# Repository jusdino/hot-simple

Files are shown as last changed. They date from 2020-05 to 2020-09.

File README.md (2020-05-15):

# hot-simple
Ender 3 Pro hot-end upgrade parts for E3D v6

*Designed in OpenScad*

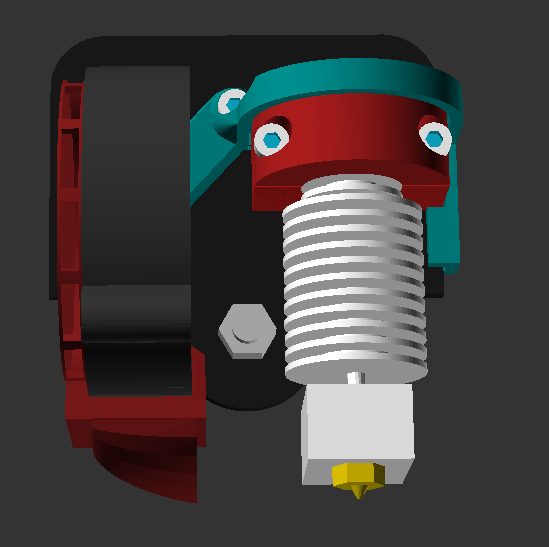
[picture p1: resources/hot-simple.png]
hot-simple


## Overview

This hot-end design is still very much a work in progress but its intent is to be simple but easy to modify. While the design is still quite incomplete, it is functional and I have been using it for a while now, with great results. I will likely eventually post this to thingiverse.com, but haven't yet as it's still too incomplete.

### Current design
The design currently uses:
 - The hot-end fan and clamp that comes with the E3D
 - A 5015 part cooling fan [like these](https://www.amazon.com/gp/product/B07DB7DLMM/ref=ppx_yo_dt_b_search_asin_title?ie=UTF8&psc=1)

## hot-end u-clamp

####  Printing:
- Material: ProtoPasta HTPLA or PETG
- Infill: 100%
- Supports: Yes 

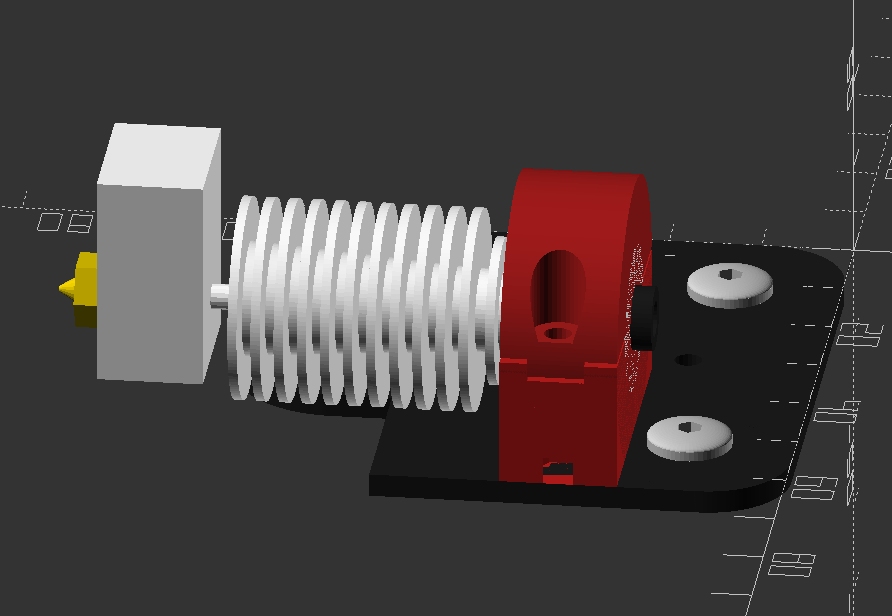
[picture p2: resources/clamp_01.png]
u-clamp


The clamp for the E3D mostly acts as an adapter, which slots over the two little pegs that hold the OEM hot-end:
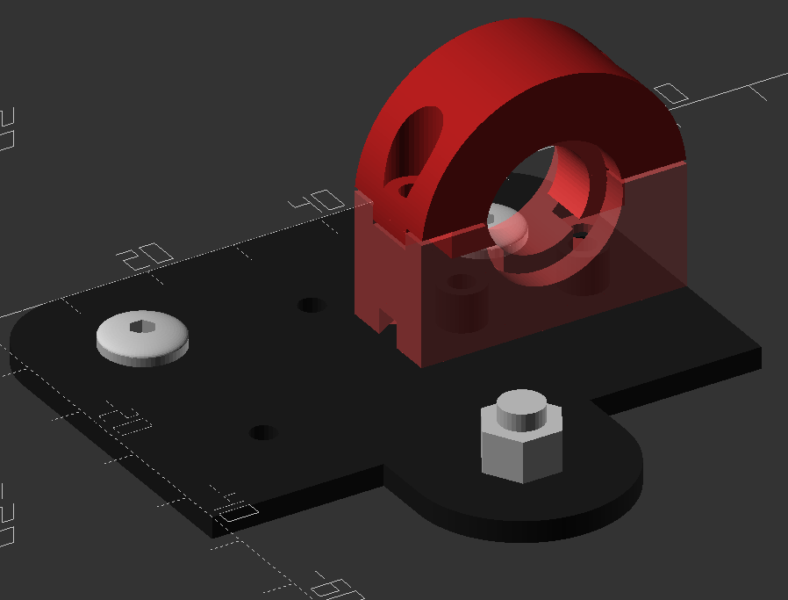
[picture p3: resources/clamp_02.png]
u-clamp


Assembly requires four screws, two M3x5 and two M3x16, and two M3 nuts
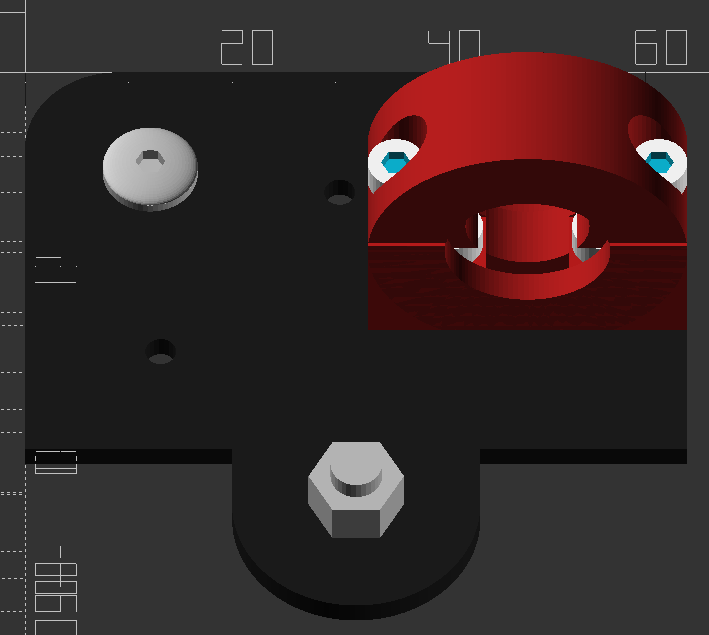
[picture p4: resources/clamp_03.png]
u-clamp with screws


The clamp fit is designed to be *very tight*. Because part of the inner collar on the U-part of the clamp has to be printed over support structure, the bottom surface tends to be a bit rough and thus makes the inner collar thickness larger than actually designed. I've taken a sharp blade and shaved that surface down until I can _just_ squeeze the U-part of the clamp all the way into the E3D collar. 

## accessory-backing

####  Printing:
- Material: ProtoPasta HTPLA
- Infill: 20%
- Supports: Yes 

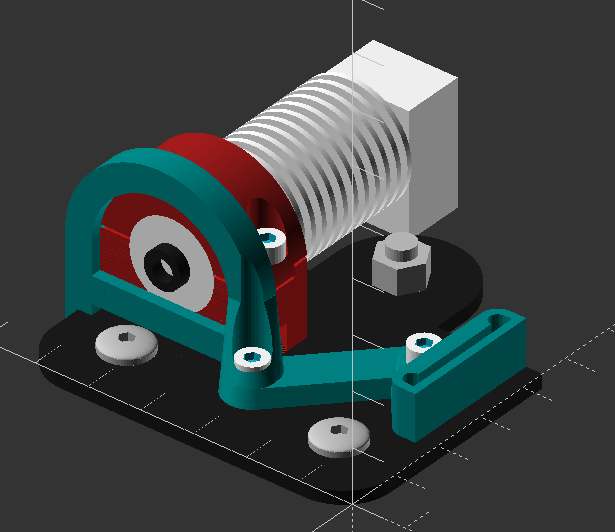
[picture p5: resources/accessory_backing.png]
accessory-backing


The accessory backing piece only has one snap-in connector for the part cooling fan. The bit that wraps around the u-clamp actually serves no purpose at the moment but will eventually be updated to include a connector for a part cooling fan on the right side of the hot-end and a top connector for a hot-end shroud.

## left-hand 5015 fan hood

####  Printing:
- Material: ProtoPasta HTPLA
- Infill: 20%
- Supports: Yes 

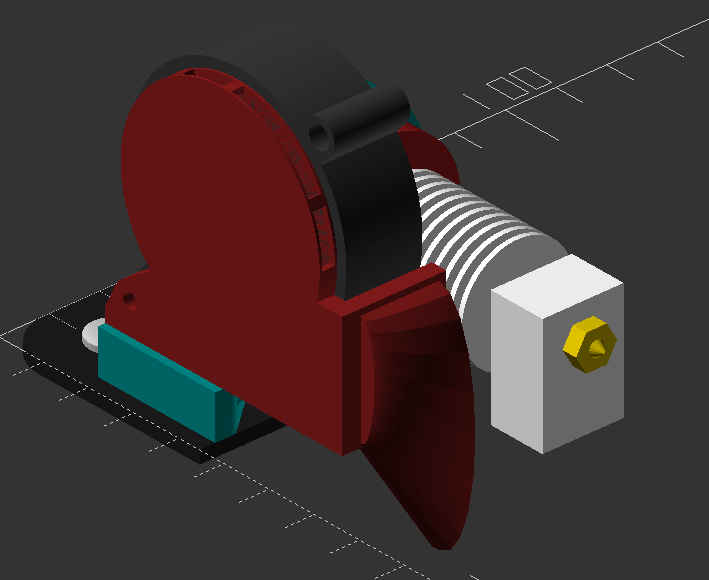
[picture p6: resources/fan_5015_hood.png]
left fan hood


This fan hood directs the intake of the fan to pull air from the cooler front of the printer and directs the output to spread across the left side in a generally rearward direction.

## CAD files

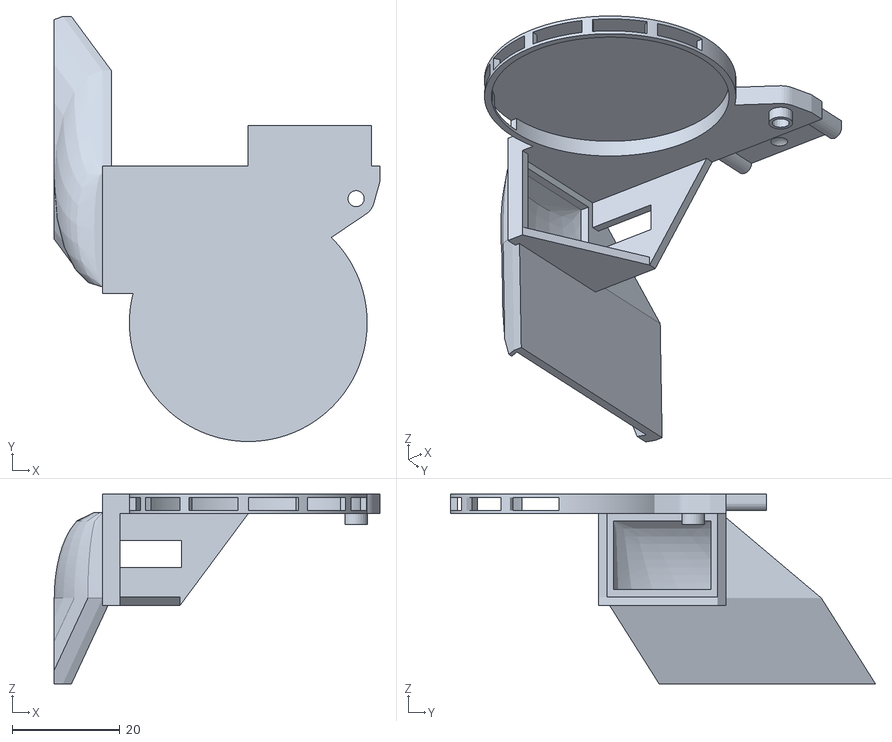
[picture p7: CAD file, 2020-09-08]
outputs/fan_5015_hood.stl
60.4 x 78.8 x 35.2

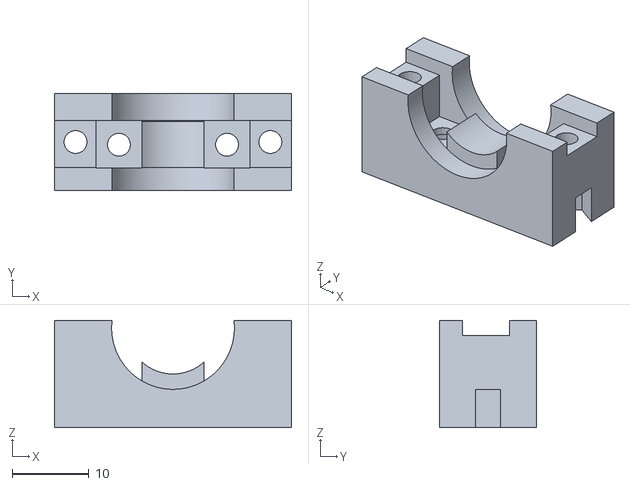
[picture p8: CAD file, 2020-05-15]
outputs/e3d_clamp_saddle.stl
30.9 x 12.7 x 14.0

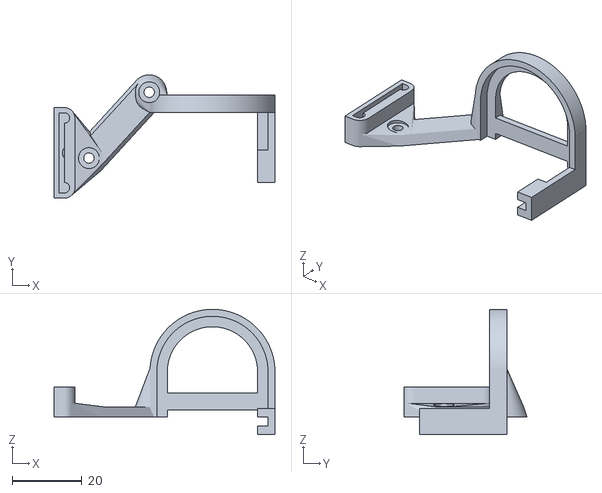
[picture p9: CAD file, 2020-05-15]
outputs/accessory_backing.stl
63.4 x 35.4 x 35.9

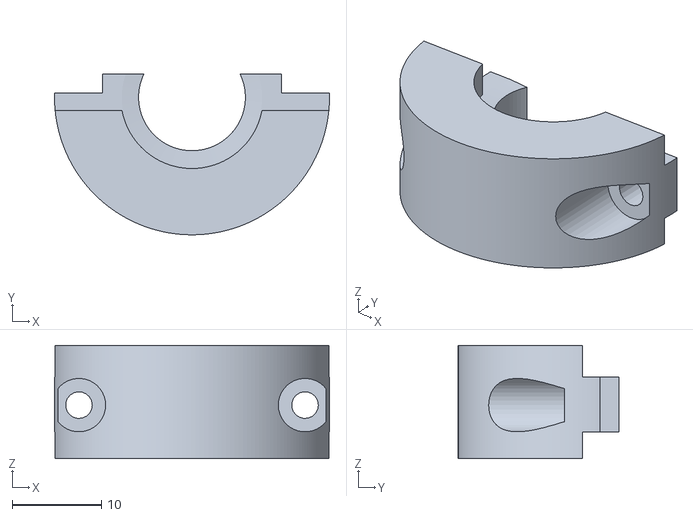
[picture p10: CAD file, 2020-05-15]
outputs/e3d_clamp_u.stl
30.9 x 18.0 x 12.7

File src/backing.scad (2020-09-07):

include <functions.scad>;
include <nutsnbolts/cyl_head_bolt.scad>;
include <e3d_clamp.scad>;
include <gantry_plate.scad>;
include <connectors.scad>;


module accessory_backing(left_connector_coords) {
  e = 0.01;
  hole_2_to_1_vec2 = [hole_1_coords[0]-hole_2_coords[0], hole_1_coords[1]-hole_2_coords[1]];
  clamp_gap = 0.5;
  saddle_diff = [saddle_dx+2*clamp_gap, saddle_dy+2*clamp_gap, saddle_dz+clamp_gap+2*e];
  saddle_diff_coords = [saddle_x-saddle_diff[0]/2, saddle_y-saddle_dy-clamp_gap/2, saddle_z];

  clamp_arm_thickness = 5;
  clamp_arm_dia = saddle_dx+clamp_arm_thickness;

  color("teal") difference() {
    union() {
      screw_hole_strap();
      left_arm();
      right_arm();
      top_bar();
      u_band();
      left_connector(left_connector_coords);
    }
    // saddle subtraction from whole arm
    translate(saddle_diff_coords) {
      translate([0, 0, -e]) {
        cube(saddle_diff);
      }
    }
    translate([0, 0, strap_thickness]) {
      translate(hole_2_coords) {
        m3_screw_hole();
      }
      translate(hole_1_coords) {
        m3_screw_hole();
      }
    }
  }

  strap_thickness = 3.0;
  module screw_hole_strap() {

    hull() {
      translate(hole_1_coords) {
        screw_hole_strap_end();
      }
      translate(hole_2_coords) {
        screw_hole_strap_end();
      }
    }
  }

  module screw_hole_strap_end() {
    strap_base_dia = 10;
    strap_top_dia = 8;
    cylinder(h=strap_thickness, d1=strap_base_dia, d2=strap_top_dia);
  }

  module left_connector(left_connector_coords) {
    part_gap = 0.1;
    connector_dz = 7.5;
    backing_thickness = 1;
    difference() {
      union() {
        hull() {
          translate(hole_1_coords) {
            screw_hole_strap_end();
          }
          translate(left_connector_coords) {
            translate([0, -pin_dy, 0]) {
              pin_slot_profile(length=4);
            }
          }
        }
        translate(left_connector_coords) {
          translate([0, -pin_dy, 0]) {
            pin_slot_profile(length=connector_dz+backing_thickness+part_gap);
          }
        }
      }
      translate(left_connector_coords) {
        translate([0, 0, connector_dz+backing_thickness+part_gap+e]) {
          rotate([180, 0, 0]) {
            pin_tab(length=connector_dz);
          }
        }
      }
    }
  }

  module left_arm() {
    hull() {
      translate(hole_2_coords) {
        screw_hole_strap_end();
      }
      translate(saddle_diff_coords) {
        translate([-(clamp_arm_thickness/2-clamp_gap), saddle_diff[1]-(clamp_arm_thickness/2+clamp_gap), 0]) {
          // left arm
          cube([clamp_arm_thickness, clamp_arm_thickness, saddle_dz]);
        }
      }
    }
  }

  module right_arm() {
    back_bar_length = 25;
    translate(saddle_diff_coords) {
      translate([saddle_diff[0]-(clamp_arm_thickness/2+clamp_gap), saddle_diff[1]-(clamp_arm_thickness/2+clamp_gap), -plate_thickness-clamp_arm_thickness/2]) {
        difference() {
          cube([clamp_arm_thickness, clamp_arm_thickness, saddle_dz+plate_thickness+clamp_arm_thickness/2]);
          translate([-e, -e, -e]) {
            cube([clamp_arm_thickness/2+clamp_gap+e, clamp_arm_thickness+2*e, plate_thickness+clamp_arm_thickness/2+e]);
          }
        }
        translate([0, -(back_bar_length-clamp_arm_thickness), 0]) {
          difference() {
            cube([clamp_arm_thickness, back_bar_length, clamp_arm_thickness+plate_thickness]);
            translate([-e, -e, clamp_arm_thickness-plate_thickness]) {
              cube([clamp_arm_thickness/2+clamp_gap+e, back_bar_length+2*e, plate_thickness+e]);
            }
          }
        }
      }
    }
  }

  module top_bar() {
    translate(saddle_diff_coords) {
      translate([-(clamp_arm_thickness/2-clamp_gap), saddle_diff[1]-(clamp_arm_thickness/2+clamp_gap), 2]) {
        cube([saddle_dx+clamp_arm_thickness, clamp_arm_thickness, clamp_arm_thickness]);
      }
    }
  }

  module u_band() {
    translate([saddle_x, saddle_y+clamp_arm_thickness/2 + clamp_gap/2, e3d_z]) {
      difference() {
        rotate([90, 0, 0]) {
          difference() {
            // band around u
            cylinder(h=clamp_arm_thickness, d=saddle_dx+clamp_arm_thickness);
            translate([0, 0, -e]) {
              cylinder(h=clamp_arm_thickness/2-clamp_gap+2*e, d=saddle_dx-clamp_arm_thickness);
            }
            translate([0, 0, clamp_arm_thickness/2-clamp_gap]) {
              cylinder(h=clamp_arm_thickness/2+clamp_gap+e, d=saddle_dx+2*clamp_gap);
            }
          }
        }
        // saddle subtraction from u band
        translate([-(saddle_dx/2+clamp_arm_thickness/2+e), -clamp_arm_thickness-e, -saddle_dx-clamp_arm_thickness-e]) {
          cube([saddle_dx+clamp_arm_thickness+2*e, clamp_arm_thickness+2*e, saddle_dx+clamp_arm_thickness]);
        }
      }
    }
  }

  module m3_screw_hole() {
    cylinder(h=saddle_dz+saddle_dx, d=6);
    translate([0, 0, -(plate_thickness+strap_thickness+e)]) {
      cylinder(h=plate_thickness+strap_thickness+2*e, d=3);
    }
  }
}

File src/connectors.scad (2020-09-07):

e=0.01;
part_gap=0.1;

pin_dia=3;
pin_dy=20;

bump_dx=0.6;
bump_dia=3;

module pin_tab_tester(length=9) {
  pin_dia=pin_dia;
  pin_dy=pin_dy;
  tab_dz=length;
  tab_dx=pin_dia/2;

  backing_thickness=2*pin_dia;

  pin_tab(length=length);
  translate([-tab_dx, -pin_dia, -backing_thickness*2]) {
    cube([backing_thickness, pin_dy+2*pin_dia, backing_thickness*2]);
  }
}

module pin_slot_tester(length) {
  box_dx=2*pin_dia;
  box_back_dz=1;
  box_dz=tab_dz+box_back_dz+part_gap;

  pin_slot(length=length);
  translate([-box_dx, -box_dx/2, -box_dx]) {
    cube([box_dx*2, pin_dy+box_dx, box_dx]);
  }
}

module pin_tab_base(length, subtractive=false) {
  pin_dia=pin_dia;
  pin_dy=pin_dy;
  tab_dz=subtractive ? length+part_gap+e : length;
  tab_dx=pin_dia/2;
  translate([-tab_dx, -pin_dia/2, 0]) {
    cube([tab_dx, pin_dy+pin_dia, tab_dz]);
  }
  cylinder(h=tab_dz, d=pin_dia);
  translate([0, pin_dy, 0]) {
    cylinder(h=tab_dz, d=pin_dia);
  }
}

module pin_tab(length) {
  pin_dia=pin_dia;
  pin_dy=pin_dy;
  tab_dz=length;
  tab_dx=pin_dia/2;

  difference() {
    pin_tab_base(length);
    translate([0, pin_dy/2, tab_dz-bump_dia]) {
      rotate([0, 0, 180]) {
        bump(h=bump_dx, d=bump_dia);
      }
    }
  }
}

module pin_slot(length) {
  box_back_dz=1;

  difference() {
    pin_slot_profile(length=length+box_back_dz+part_gap);
    translate([0, 0, box_back_dz]) {
      pin_tab_base(subtractive=true);
    }
  }
  translate([0, pin_dy/2, bump_dia]) {
    rotate([0, 0, 180]) {
      bump(h=bump_dx, d=bump_dia);
    }
  }
}

module pin_slot_profile(length) {
  box_dx=2*pin_dia;
  box_dz=length;
  union() {
    cylinder(h=box_dz, d=box_dx);
    translate([0, pin_dy, 0]) {
      cylinder(h=box_dz, d=box_dx);
    }
    translate([-pin_dia, 0, 0]) {
      cube([box_dx, pin_dy, box_dz]);
      translate([0, -box_dx/2, 0]) {
        cube([box_dx/2, pin_dy+box_dx, box_dz]);
      }
    }
  }
}

module bump(h, d) {
  dia=(pow(d/2, 2) + pow(h, 2))/(2*h)*2;
  inset=dia/2-h;
  difference() {
    translate([-inset, 0, 0]) {
      sphere(d=dia);
    }
    translate([-dia-e, -dia/2, -dia/2]) {
      cube([dia, dia, dia]);
    }
  }
}

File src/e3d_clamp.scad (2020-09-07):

include <nutsnbolts/cyl_head_bolt.scad>;
include <e3d_v6.scad>;
include <gantry_plate.scad>;

e = 0.01;

collar_total_dy = collar_seg_1_dy+collar_seg_2_dy+collar_seg_3_dy;
collar_seg_2_mid_y = collar_seg_1_dy+collar_seg_2_dy/2;
saddle_overreach = 1;

peg_avg_x = (peg_1_coords[0]+peg_2_coords[0])/2;
peg_avg_y = (peg_1_coords[1]+peg_2_coords[1])/2;
peg_dx = (peg_2_coords[0]-peg_1_coords[0]);
peg_screw_space = 1;
peg_hole_dia = peg_dia + 0.3;
peg_hole_dz = peg_dz + 0.5;

saddle_dx = (plate_width-peg_avg_x)*2;
saddle_dy = collar_total_dy;
saddle_dz = gill_dia/2 + 2 + saddle_overreach;

saddle_x = peg_avg_x;
saddle_y = peg_avg_y+collar_seg_2_mid_y;
saddle_z = 0;
saddle_coords = [saddle_x, saddle_y, saddle_z];
saddle_wedge_dy = 0.16;

e3d_dz = saddle_dz-saddle_overreach;
e3d_z = e3d_dz+saddle_z;

key_dz = 2;

nut_slot_size = 5.6;
nut_slot_dz = 5;
clamp_screw_inset = 2.75;
clamp_screw_head_hole_dia = 6;

u_gap = 0.5;
u_overreach = e3d_dz-peg_hole_dz-peg_screw_space-4.5;
u_key_inset = (saddle_dx - peg_dx)/2 - collar_seg_2_dy/2;
u_screw_dz = 4;

module e3d_clamp_saddle(coords) {
  color([0.7, 0.1, 0.1]) {
    translate(coords) {
      peg_cut_outs([-peg_dx/2, -collar_seg_1_dy-collar_seg_2_dy/2, 0]) {
        peg_cut_outs([peg_dx/2, -collar_seg_1_dy-collar_seg_2_dy/2, 0]) {
          e3d_collar_cut_out([0, 0, e3d_dz]) {
            translate([-(saddle_dx)/2, -saddle_dy, 0]) {
              difference() {
                // main block
                cube([saddle_dx, saddle_dy, saddle_dz]);
                // key
                translate([-e, collar_seg_3_dy, saddle_dz-key_dz]) {
                  cube([saddle_dx+2*e, collar_seg_2_dy+saddle_wedge_dy, key_dz+e]);
                }
                // screw/nut slots
                translate([clamp_screw_inset, saddle_dy/2, -e]) {
                  rotate([0, 0, 30]) {
                    cylinder($fn=6, d=nut_slot_size*2/sqrt(3), h=nut_slot_dz);
                  }
                  cylinder(d=3, h=saddle_dz+2*e);
                }
                translate([saddle_dx-clamp_screw_inset, saddle_dy/2, -e]) {
                  rotate([0, 0, 30]) {
                    cylinder($fn=6, d=nut_slot_size*2/sqrt(3), h=nut_slot_dz);
                  }
                  cylinder(d=3, h=saddle_dz+2*e);
                }
              }
            }
          }
        }
      }
    }
  }
}

module e3d_clamp_u(coords) {
  translate(coords) {
    translate([0, 0, e3d_dz]) {
      color([0.6, 0.1, 0.1]) {
        e3d_collar_cut_out([0, 0, 0]) {
          difference() {
            // main cylinder
            rotate([90, 0, 0]) {
              cylinder(h=saddle_dy, d=saddle_dx);
            }
            // bottom seg 2 lowest subtraction
            translate([-saddle_dx/2-e, -saddle_dy-e, -(u_overreach+saddle_dx)]) {
              cube([saddle_dx+2*e, saddle_dy+2*e, saddle_dx]);
            }
            // bottom seg 2 key subtractions
            translate([-saddle_dx/2-e, -collar_seg_1_dy-collar_seg_2_dy-e, saddle_overreach+u_gap-key_dz-u_overreach]) {
              cube([u_key_inset, collar_seg_2_dy+saddle_wedge_dy+2*e, u_overreach]);
            }
            translate([saddle_dx/2+e-u_key_inset, -collar_seg_1_dy-collar_seg_2_dy-e, saddle_overreach+u_gap-key_dz-u_overreach]) {
              cube([u_key_inset, collar_seg_2_dy+saddle_wedge_dy+2*e, u_overreach]);
            }
            translate([-saddle_dx/2-e, -saddle_dy-e, -saddle_dx-key_dz+saddle_overreach+u_gap]) {
              // bottom seg 1 subtraction
              translate([0, 0, -e]) {
                cube([saddle_dx+2*e, collar_seg_3_dy+e, saddle_dx+key_dz+e]);
              }
              // bottom seg 3 subtraction
              translate([0, collar_seg_3_dy+collar_seg_2_dy+saddle_wedge_dy+e, -e]) {
                cube([saddle_dx+2*e, collar_seg_1_dy-saddle_wedge_dy+e, saddle_dx+key_dz+e]);
              }
            }
            // screw cuts
            translate([-saddle_dx/2+clamp_screw_inset, -collar_seg_1_dy-collar_seg_2_dy/2, -u_gap-e]) {
              cylinder(h=saddle_dx, d=3);
              translate([0, 0, u_screw_dz]) {
                cylinder(h=saddle_dx, d=clamp_screw_head_hole_dia);
              }
            }
            translate([saddle_dx/2-clamp_screw_inset, -collar_seg_1_dy-collar_seg_2_dy/2, -u_gap-e]) {
              cylinder(h=saddle_dx, d=3);
              translate([0, 0, u_screw_dz]) {
                cylinder(h=saddle_dx, d=clamp_screw_head_hole_dia);
              }
            }
          }
        }
      }
    }
  }
}

module e3d_collar_cut_out(coords) {
  difference() {
    children();
    translate(coords) {
      rotate([90, 0, 0]) {
        // seg 1
        translate([0, 0, -e]) {
          cylinder(h=collar_seg_1_dy-saddle_wedge_dy+e, d=collar_outer_dia);
        }
        translate([0, 0, collar_seg_1_dy]) {
          // seg 1 wedge
          translate([0, 0, -saddle_wedge_dy-e]) {
            cylinder(h=saddle_wedge_dy+e, d1=collar_outer_dia, d2=collar_inner_dia);
          }
          // seg 2
          translate([0, 0, -e]) {
            cylinder(h=collar_seg_2_dy+2*e, d=collar_inner_dia);
          }
          // seg 3
          translate([0, 0, collar_seg_2_dy-e]) {
            cylinder(h=collar_seg_3_dy+2*e, d=collar_outer_dia);
          }
        }
      }
    }
  }
}

module peg_cut_outs(coords) {
  difference() {
    children();
    translate(coords) {
      // cube screw slot
      translate([-collar_seg_2_dy/2, -collar_seg_2_dy/2-e, peg_hole_dz+peg_screw_space]) {
        cube([collar_seg_2_dy, collar_seg_2_dy+saddle_wedge_dy+2*e, saddle_dz-peg_hole_dz-peg_screw_space+e]);
      }
      // screw hole
      translate([0, 0, peg_hole_dz-e]) {
        cylinder(h=peg_screw_space+2*e, d=3);
      }
      // peg hole
      translate([0, 0, -e]) {
        cylinder(h=peg_hole_dz+2*e, d=peg_hole_dia);
      }
    }
  }
}

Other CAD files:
src/e3d_v6.scad
src/fan_4010.scad
src/fan_4010_hoods.scad
src/fan_5015.scad
src/fan_5015_hoods.scad
src/functions.scad
src/gantry_plate.scad
src/hot-simple.scad

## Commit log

2020-04-10 Add working files
    [backing.scad, connectors.scad, e3d_clamp.scad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]
2020-05-15 Organize and document
    [accessory_backing.stl, backing.scad, connectors.scad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]
2020-09-07 get rid of all those CAPS vars
    [backing.scad, connectors.scad, e3d_clamp.scad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]
2020-09-08 Try alternative extended nozzle
    [fan_5015_hoods.scad, fan_5050_hood.stl]
2020-09-08 Some tweaks after printing
    [fan_5015_hood.stl, fan_5015_hoods.scad, fan_5050_hood.stl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]
